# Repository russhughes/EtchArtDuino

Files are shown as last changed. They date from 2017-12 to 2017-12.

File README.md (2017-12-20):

# EtchArtDuino

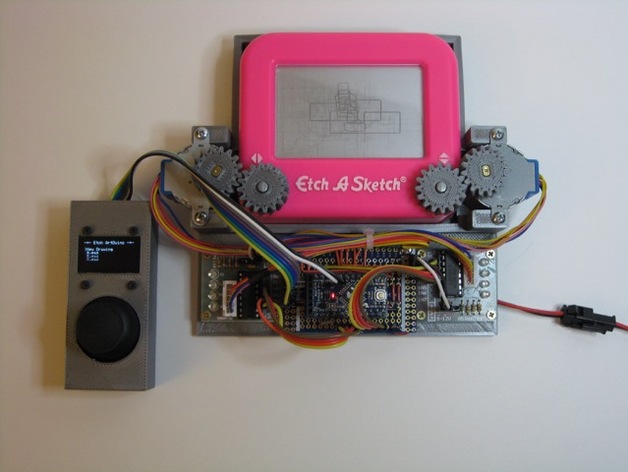
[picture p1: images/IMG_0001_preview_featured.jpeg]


## Description

Arduino powered Etch A Sketch with joystick controller and SD card storage. Arduino source included in EtchArtDuino folder.  The EtchArtDuinoSimple folder contains a simplified version of the software that just allows you to draw using the joystick that is usefull for younger children.

## Instructions

Sorry, not a lot of build details here. I just built as I went with parts I had on hand in order to play with the steppers. It's one of my first OpenSCAD and Arduino projects so the code is, what it is. Don't judge it too harshly.  

The menu system is pretty basic but it allows you to create and save a new drawing and redraw or delete an existing drawing.  

Joystick| Menu usage  
:------:|:----------:
Up/Down | Moves cursor  
Left | Back/Cancel  
Right or Press | Select  

Joystick Drawing usage is as you would expect:up, down, left, right. Press the joystick to end the drawing. It will ask if you are done, select yes to save and exit the drawing or select no to continue drawing.   

Since the Etch ArtDuino has no way of knowing where the drawing stylus is at the beginning of a drawing, the display will ask you to choose a starting position (upper left or right, lower left or right, or the center) and then ask you to move the stylus there then press the joystick. It will save the starting position as the first byte of the file so it can prompt you to move the stylus to the correct position when redrawing the file.  

Drawings are stored on a SD card using the Arduino SD library. You can cheat and create the files on a computer. The files must have an ".eas" extension and be in the root directory.  

    The file format is:  
	
	1st byte is binary and contains the suggested starting position   
		1: Upper Left  
		2: Upper Right  
		3: Lower Left  
		4: Lower Right  
		5: Center  

	The rest of the file is a string of single character   
    drawing commands  

		u: move up  
		d: move down  
		l: move left  
		r: move right  

    An example of a tiny 3x3 box would be:  
    (binary value of 1,2,3,4 or 5)rrrdddllluuu  

### Wiring chart
  
Arduino | Connection
:------:|:---------:
VCC	 | +5V Supply  
GND	 | Ground  
D2	| Horiz/Left Stepper IN1  X-axis  
D3	| Horiz/Left Stepper IN2  
D4	| Horiz/Left Stepper IN3  
D5	| Horiz/Left Stepper IN4  
D6	| Vert/Right Stepper IN1 Y-axis  
D7	| Vert/Right Stepper IN2  
D8	| Vert/Right Stepper IN3  
D9	| Vert/Right Stepper IN4  
D10	 | SPI SS SD Card  
D11	 | SPI MOSI SD Card  
D12	 | SPI MISO SD Card  
D13 | SPI SCK SD Card  
A0 | 	Joystick VX  
A1 | 	Joystick VY  
A2 | 	Joystick Button  
A4 | 	I2C SDA		OLED  
A5 | 	I2C SCL		OLED  

### Parts List:  
Qty | Description
:--:|------------
1 | 3D Printed EtchArtDuino.stl  
1 | 3D Printed gears.stl  
1 | 3D Printed joystick.stl  
1 | Pocket Etch A Sketch  
2 | 28BYJ-48 5V DC 4-Phase 5-Wire + ULN2003 Driver Board (ebay/amazon)  
1 | Catalex microsd card adapter (ebay/electrodragon/amazon)  
1 | Parallax.com Circuit Overlay Board (Part #32999) 
1 | Arduino Pro Mini 328 - 5V/16MHz (sparkfun)  
1 | 0.96" I2C 128X64 OLED (ebay/electrodragon/amazon)  
1 | PS2 Joystick Module marked "Keyes_SJoys" (ebay/electrodragon/amazon)
1 | 5v Power supply and mating connector.  
  Miscellaneous | 2mm screws and nuts. 
Miscellaneous | jumper wires  

### Additional SCAD Sources:  

Parkinbot's Excellent Gear Library http://www.thingiverse.com/thing:636119  

### Additional Arduino Libraries:  

SSD1306Ascii	https://github.com/greiman/SSD1306Ascii  
Bounce2  https://github.com/thomasfredericks/Bounce2

### License
http://www.thingiverse.com/thing:948117
licensed under the Creative Commons - Attribution - Share Alike license. http://creativecommons.org/licenses/by-sa/3.0/

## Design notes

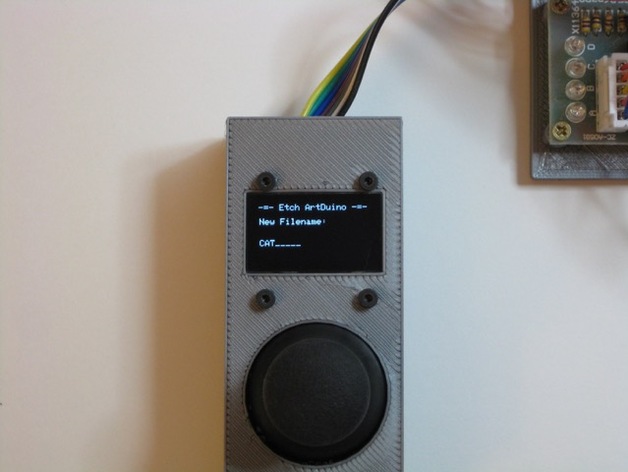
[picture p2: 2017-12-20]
images/IMG_0015_preview_featured.jpeg

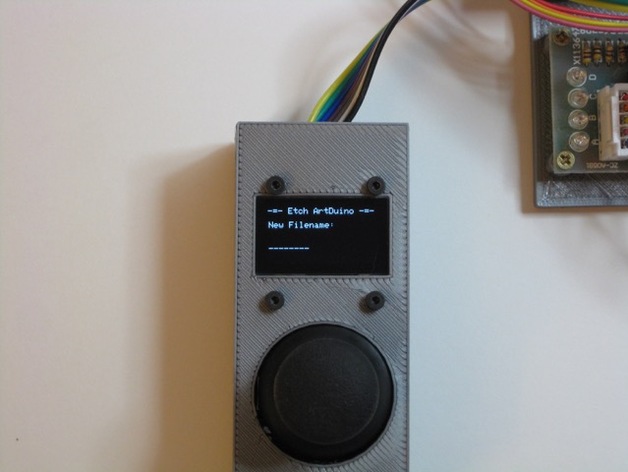
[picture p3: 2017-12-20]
images/IMG_0014_preview_featured.jpeg

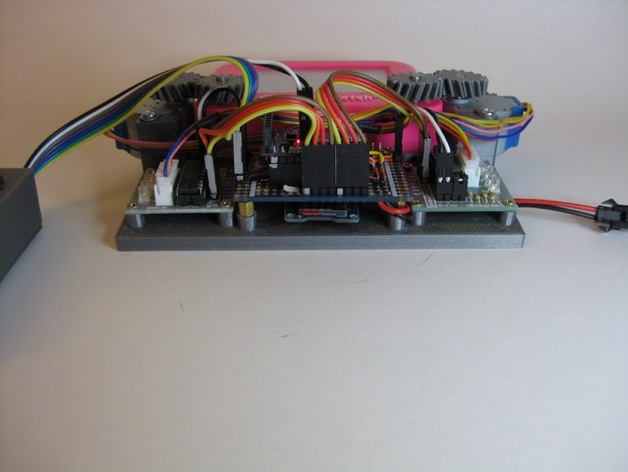
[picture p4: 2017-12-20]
images/IMG_0011_preview_featured.jpeg

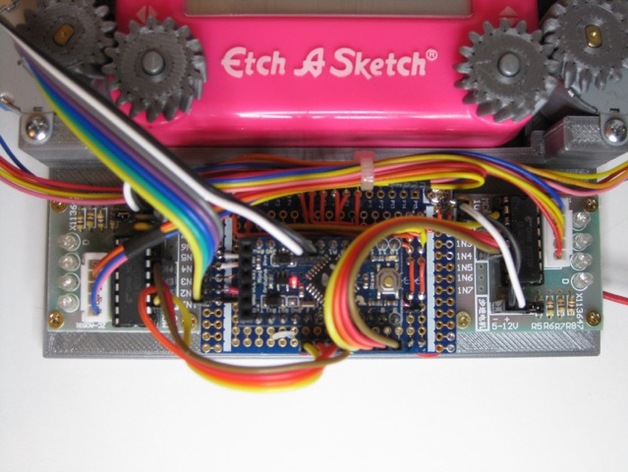
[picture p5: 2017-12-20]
images/IMG_0004_preview_featured.jpeg

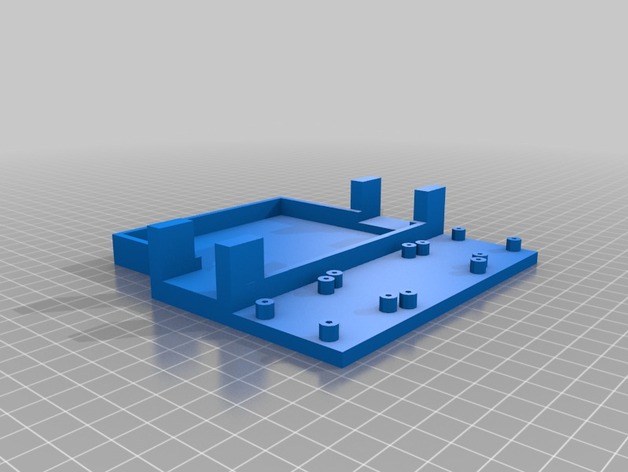
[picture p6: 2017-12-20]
images/EtchArtDuino_preview_featured.jpg

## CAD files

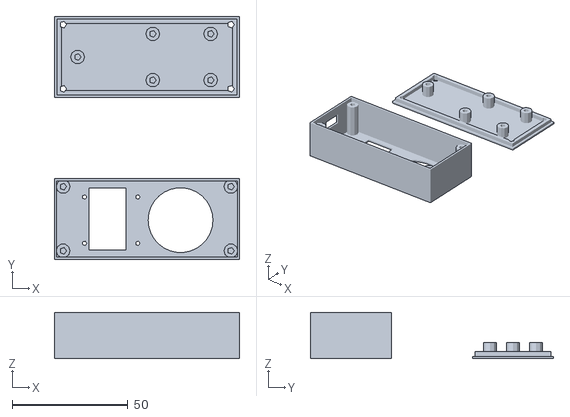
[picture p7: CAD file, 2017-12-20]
3D Printer Files/joystick.stl
80.0 x 105.0 x 20.0

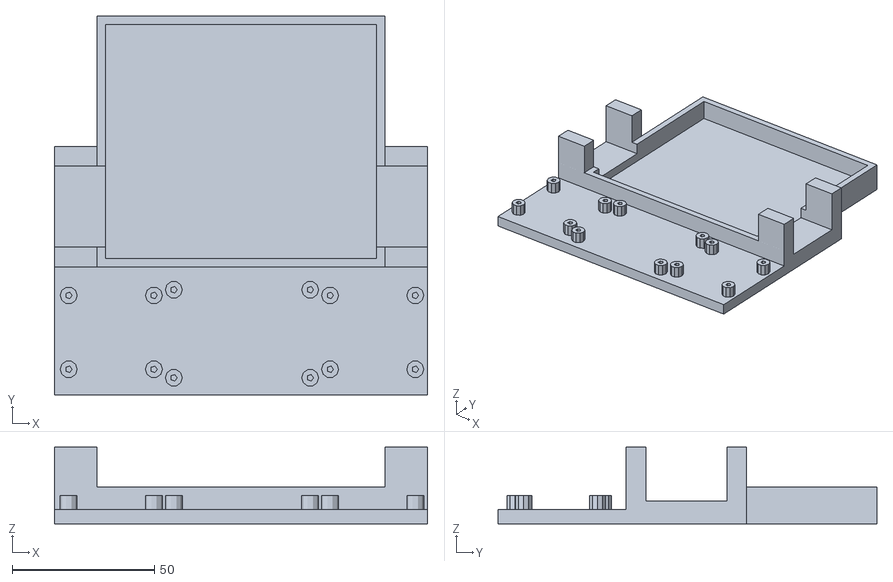
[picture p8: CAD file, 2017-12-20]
3D Printer Files/EtchArtDuino.stl
131.3 x 133.3 x 27.0

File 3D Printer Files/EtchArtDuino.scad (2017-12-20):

height=10;              // height of pocket
width=95.3;             // width of pocket
length=82.3;            // length of pocket
thick=3;                // thickness of wall
supports=5;             // support shelf thickness 

owidth=width+thick*2;   // pocket outside width
olength=length+thick*2; // pocket outside length
oheight=height+thick;   // pocket outside height

so_d = 6;               // stand off diameter
shelf_w = owidth+15+15;          // board shelf width
shelf_l = 45;           // board shelf length

// board stand off

module stand_off()
{
    translate([0,0,-1])
    {
        difference() 
        {
            cylinder(h=6,d=so_d, center= false);
            cylinder(h=6,d=so_d/2.5, center= false);
        }
    }
}

// Servo board holder

module servo_board()
{
    //cube([36, 38, 5]);
    translate([3,9,5]) stand_off();
    translate([3,35,5]) stand_off();
    translate([33,9,5]) stand_off();
    translate([33,35,5]) stand_off();
}

// Cpu board holder

module cpu_board()
{
    //cube([56, 40, 6]);
    translate([4,6,5]) stand_off();
    translate([56-4,6,5]) stand_off();
    
    translate([4,37,5]) stand_off();
    translate([56-4,37,5]) stand_off();
    
}

// Board shelf

module shelf()
{
    translate([0,0,0]) 
    {
        cube([shelf_w, shelf_l, 5]);
        translate([2,0,0]) servo_board();
        translate([130-33-3, 0, 0]) servo_board();
        translate([38, 0, 0]) cpu_board();
    }
}


difference () {
union() {
difference()
{
    cube(size = [owidth,olength,oheight], center = false);
    translate([thick,thick,thick+1]) 
        cube(size = [width,length,height+4], center = false);
}

// left servo base
translate([-15,0,0])
    cube([15,42.5, oheight], center = false);

// left servo mount bottom tower
translate([-15,.05,0])
    cube([15,7, oheight+14], center = false);

// left servo mount top tower
translate([-15,28+7.5,0])
    cube([15,7, oheight+14], center = false);

// left servo controller board
//translate([-5,56.3,0])
//    cube([5,32, supports], center = false);

// right servo base
translate([owidth,0,0])
    cube([15,42.5, oheight], center = false);
    
// right servo mount bottom tower
translate([owidth,.05,0])
    cube([15,7, oheight+14], center = false);
    
// right servo mount top tower
translate([owidth,28+7.5,0]) 
    cube([15,7, oheight+14], center = false);
}

// left servo base servo cutout
translate([-15,7,oheight-5])
    cube([15+thick,28.5, 5], center = false);

// right servo base servo cutout
translate([owidth-thick,7, oheight-5])
    cube([15+thick,28.5, 5], center = false);
}

translate([-15,-shelf_l, 0]) 
    shelf();

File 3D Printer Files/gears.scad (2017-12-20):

// library for parametric involute gears 
// Author: Rudolf Huttary, Berlin 
// Jan 2015

$fn = 500; 
iterations = 10; // increase for enhanced resolution beware: large numbers will take lots of time!

// default values
// z = 10; // teeth - beware: large numbers may take lots of time!
// m = 1;  // modulus
// x = 0;  // profile shift
// h = 4;  // face_width	respectivly axial height
// w = 20; // profile angle
// clearance  // assymmetry of tool to clear tooth head and foot
//    = 0.1; // for external splines
//    = -.1  // for internal splines 
// w_bevel = 45; // axial pitch angle
// w_helix = 45; // radial pitch angle 

// use this prototype:
// gear(m = modulus, z = Z, x = profile_shift, w = alpha, h = face_width);

di = 20; 
knob_r = 2.5-.125;  // took away .2
knob_h = 4;
servo_r = 2.5; // was 2.45 added .250/2 added .250/2 again
servo_h = 4;

// 2 Gears for knobs 

module knob_gear()
{
    difference(){       
        gear_helix(z = 16, m = 1.2, h = knob_h, w_helix = -20, clearance = 0.1); 
        cylinder(h=knob_h,r=knob_r, center= true);
    }
}

translate([di, di, knob_h])     knob_gear();
translate([-di, di, knob_h])    knob_gear();


// 2 gears for servos

module servo_gear() {
    difference(){   
        gear_helix(z = 16, m = 1.2, h = servo_h, w_helix = 20, clearance = 0.1); 
        cylinder(h=servo_h,r=servo_r, center= true);
    }
    
    // keyway
    
    translate([1.7,0-4, -servo_h/2]) cube(size=[3,8,servo_h]);
    translate([-4.7,0-4, -servo_h/2]) cube(size=[3,8,servo_h]);
}

translate([di, -di, servo_h])       servo_gear();
translate([-di, -di, servo_h])      servo_gear();

//
// Abandon hope all ye who edit past this comment !!!
//

// === modules for internal splines
module Gear(m = 1, z = 10, x = 0, h = 4, w = 20, D = 13, clearance = -.1, center = true) 
{
   difference()
   {
		cylinder(r = D/2, h = h, center = center);
		gear(m, z, x, h+1, w, center = center, clearance = clearance); 
	}
}

module Gear_herringbone(m = 1, z = 10, x = 0, h = 4, w = 20, w_helix = 45, D = 13, clearance = -.1) 
{
   difference()
   {
		cylinder(r = D/2, h = h-.01, center = true); // CSG!
		gear_herringbone(m, z, x, h, w, w_helix, clearance = clearance); 
	}
}

module Gear_helix(m = 1, z = 10, x = 0, h = 4, w = 20, w_helix = 45, D = 13, clearance = -.1) 
{
   difference()
   {
		cylinder(r = D/2, h = h-.01, center = true); // CSG!
		gear_helix(m, z, x, h, w, w_helix, clearance = clearance); 
	}
}

module Gear_bevel(m = 1, z = 10, x = 0, h = 4, w = 20, w_bevel = 45, w_helix = 0, D = 13, clearance = -0.1, center = true)
{
   rotate([0, 180, 0])
   difference()
   {
		cylinder(r = D/2, h = h-.01, center = true); // CSG!
		gear_bevel(m, z, x, h, w, w_bevel, w_helix, clearance = clearance, center = center); 
	}
}


// === modules for external splines
module gear_herringbone(m = 1, z = 10, x = 0, h = 4, w = 20, w_helix = 45, clearance = 0.1)
{
   for(i=[0, 1])
   mirror([0,0,i])
   translate([0, 0, -0.001]) // CSG!
   gear_helix(m, z, x, h/2, w, w_helix, center = false, clearance = clearance); 
}

module gear_helix(m = 1, z = 10, x = 0, h = 4, w = 20, w_helix = 45, center = true, clearance = 0.1)
{
   gear_info(m, z, x, h, w, w_helix, 0, clearance); 
	r_wk = m*z/2 + x; 
   tw = (h * w_helix)/ r_wk  ; 
	linear_extrude(height = h, center = center, twist = tw, slices = ceil(10*h), convexity = z)
   gear_(m, z, x, w, clearance); 
}

module gear_bevel(m = 1, z = 10, x = 0, h = 4, w = 20, w_bevel = 45, w_helix = 0, clearance = 0.1, center = true)
{
   gear_info(m, z, x, h, w, 0, w_bevel, clearance); 
	r_wk = m*z/2 + x; 
   sc = (r_wk-tan(w_bevel)*h)/r_wk; 
   tw = (h * w_helix)/ r_wk  ; 
	linear_extrude(height = h, center = center, twist = tw, scale = [sc, sc], convexity = z)
   gear_(m, z, x, w, clearance); 
}

module gear(m = 1, z = 10, x = 0, h = 4, w = 20, clearance = 0.1, center = true)
{
   gear_info(m, z, x, h, w, clearance = clearance); 
	linear_extrude(height = h, center = center, convexity = z)
   gear_(m, z, x, w, clearance); 
}

module gear_info(m = 1, z = 10, x = 0, h = 0, w = 20, helix_angle = 0, bevel_angle = 0, clearance = 0.1)
{
  	r_wk = m*z/2 + x; 
   	dy = m;  
  	r_kk = r_wk + dy;   
  	r_fk = r_wk - dy;  
  	r_kkc = r_wk + dy *(1-clearance/2);   
  	r_fkc = r_wk - dy *(1+clearance/2);  
   echo(str ("modulus = ", m)); 
   echo(str ("Z = ", z)); 
   echo(str ("profile angle = ", w, "°")); 
   echo(str ("d = ", 2*r_wk)); 
   echo(str ("d_outer = ", 2*r_kk, "mm")); 
   echo(str ("d_inner = ", 2*r_fk, "mm")); 
   echo(str ("height = ", h, "mm")); 
   echo(str ("clearance factor = ", clearance)); 
   echo(str ("d_outer_cleared = ", 2*r_kkc, "mm")); 
   echo(str ("d_inner_cleared = ", 2*r_fkc, "mm")); 
   echo(str ("helix angle = ", helix_angle, "°")); 
   echo(str ("bevel angle = ", bevel_angle, "°")); 
   echo("================"); 
}

// === from here 2D stuff == 
module gear_(m = 1, z = 10, x = 0, w = 20, clearance = 0.1)
{
  	r_wk = m*z/2 + x; 
   	dy = m;  
  	r_fkc = r_wk - dy *(1+clearance/2)+.01;  //.01 has numerical reason!
   union()
	{
		for(i = [0:z-1]) 
			rotate([0, 0, i*360/z])
			Tooth(m, z, x, w, clearance);
     circle(r_fkc); 
	}
}

module Tooth(m = 1, z = 10, x = 0, w = 20, clearance = 0)
{
	union()
	{
		Tooth_half(m, z, x, w, clearance); 
		mirror([1, 0, 0])
		Tooth_half(m, z, x, w, clearance); 
	}
}

module Tooth_half(m = 1, z = 10, x = 0, w = 20, clearance = 0)
{
  	r_wk = m*z/2 + x; 
  	r_fkc = r_wk - m *(1+clearance/2);   
	du = z*m/360*PI; 
	dw = 360/z; 
 	difference()
	{
		cake_piece(m, z, x, w, clearance); 
      	union()
		{
			for(i = [-dw:dw/iterations:dw])
			  rotate([0, 0, i])
			  translate([i*du, 0, 0])
			Tool(m, z, x, w, clearance); 
		}
	}
}

module Tool(m = 1, z = 10, x = 0, w = 20, clearance = 0)
{
   p = m*PI; 
   dy = 2*m;  
   dx = dy * tan(w);  
   ddx = dx/2 * clearance/2; 
   ddy = dy/2 * clearance/2; 
	r_wk = m*z/2 + x; 
   polygon(points = [
		[0, r_wk+dy], 
		[0, r_wk+dy/2-ddy], 
		[p/4-dx/2 + ddx, r_wk+dy/2 - ddy], 
		[p/4+dx/2 + ddx, r_wk-dy/2 - ddy], 
		[p/2,            r_wk -dy/2 - ddy],
		[p/2,            r_wk +dy/2 - ddy],
		[p/2,            r_wk+dy], 
		]);  
}

module cake_piece(m = 1, z = 10, x = 0, w = 20, clearance = 0)
{
	$fn = 100; 
	r_wk = m*z/2 + x; 
   p = m*PI; 
   dy = p/2*cos(w);  
   r_kk = r_wk + dy*(1+clearance);   
   intersection()
   {
     half_circle(r_kk); 
     rotate([0, 0, 180])
     rotate([0, 0, -181/z]) // 181 has numerical reason!
     half_circle(r_kk); 
	}
}

module half_circle(r)
{
	intersection()
  	{
		circle(r = r); 
     translate([0, -r, 0])
     square(2*r); 
	}
}

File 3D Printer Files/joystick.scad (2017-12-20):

length = 80;            // box lenght
width = 35;             // box width
height = 20;            // box, height

joy = 28;               // joystick hole diameter
joy_offset = 15;         // x offset for joysitck

so_d = 6;               // stand off diameter

disp_offset = 15;        // display offset from end
disp_w = 27;            // display width
disp_l =16;             // display length

disp_hdist = 20;        // display horizontal mounting hole distance
disp_vdist =  23;       // display vertial mount hole distance

module standoff(sh=6, sd=6)
{
    translate([0,0,-1])
    {
        difference() 
        {
            // standoff
            
            cylinder(h=sh,d=sd, center= false);
            
            // screw hole
            
            cylinder(h=sh,d=sd/2, center= false);
        }
    }
}

module base() 
{
    // four standoffs for joystick (25x20mm) 
    
    translate([0,0,0])      standoff(sh=7, sd=so_d);
    translate([25,0,0])     standoff(sh=7, sd=so_d);
    translate([0,20,0])     standoff(sh=7, sd=so_d);
    translate([25,20,0])    standoff(sh=7, sd=so_d);
}    

module wire()
{
    cube([2,10,5]);
}

module box()
{
    difference()
    {
        // outer shell
        
        cube([length, width, height]);
        
        // inner wall
        
        translate([1,1,1])
            cube([length-2, width-2, height]);
        
        // wire hole
        
        translate([0,width/2-5, 10])
            wire();

        // Joystick hole
        
        translate([length/2+joy_offset-0.5,width/2-0.5,0])
            cylinder(h=2,d=joy, center=false);
        
        // display hole
        
        translate([disp_offset ,width/2-disp_w/2,0])    cube([disp_l,disp_w,1]);
        
        // display mounting holes
        
        translate([disp_offset ,width/2-disp_w/2,0])
        {
            translate([-2,3,0])     cylinder(h=1,d=2, center= false);
            translate([-2,23,0])    cylinder(h=1,d=2, center= false);
            translate([-2+23,3,0])  cylinder(h=1,d=2, center= false);
            translate([-2+23,23,0]) cylinder(h=1,d=2, center= false);
        }
    }
    
    // corner standoffs
    
    translate([5-1.25,5-1.25,1]) standoff(sh=height-2.1, sd=so_d);
    translate([5-1.25,30+1.5,1]) standoff(sh=height-2.1, sd=so_d);
    
    translate([length-3.75,5-1.25,1]) standoff(sh=height-2.1, sd=so_d);
    translate([length-3.75,30+1.5,1]) standoff(sh=height-2.1, sd=so_d);
    
    // proto board standoff
    

}

module bottom()
{
    difference()
    {
        // bottom
        
        union() 
        {
            cube([length, width, 1]);
        
            // joystick mounting base

            translate([length/2-25/2+joy_offset, width/2-20/2,1]) 
                base();
            
            // protoboard standoff
            
            translate([10,width/2,1]) standoff(7, sd=so_d);

    
            // lengthwise bottom ridges
    
            translate([1.1,1.1,1])       cube([length-2.2, 2, 2]);
            translate([1.1,width-3.1,1]) cube([length-2.2, 2, 2]);
    
            // horizontal botton ridges
    
            translate([1.1,1.1,1])         cube([2, width-2.2, 2]);
            translate([length-3.1,1.1,1])  cube([2, width-2.2, 2]);
        }  
        
        // standoff screw holes
        
        translate([5-1.25,5-1.25,0])        cylinder(h=5,d=so_d/2, center= false);
        translate([5-1.25,30+1.5,0])        cylinder(h=5,d=so_d/2, center= false);
        translate([length-3.75,5-1.25,0])   cylinder(h=5,d=so_d/2, center= false);
        translate([length-3.75,30+1.5,0])   cylinder(h=5,d=so_d/2, center= false);
    }

   
}

box();
translate([0, width*2, 0])   bottom();

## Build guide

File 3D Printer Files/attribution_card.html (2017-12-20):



# Etch ArtDuino by PawArmy

## Published on July 30, 2015

### www.thingiverse.com/thing:948117

####   

#### Creative Commons - Attribution - Share Alike

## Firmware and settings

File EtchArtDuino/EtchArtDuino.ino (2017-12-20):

/*
 * Etch-Art-Duino
 *  
 * Russ Hughes, July 2015 russ@owt.com 
 * Creative Commons - Attribution - Non-Commercial license.
 * 
 */

#include <SPI.h>
#include <SD.h>
#include <Wire.h>
#include "SSD1306Ascii.h"
#include "SSD1306AsciiWire.h"
#include <Stepper.h>
#include <Bounce2.h>
#include "menu.h"

// display 
#define I2C_ADDRESS 0x3C
SSD1306AsciiWire oled;
#define DISPLAY_LINES 8
#define MENU_LINES 6

// sd card

const int PIN_SD_CS = 10;
const bool ALLOW_WIPE = false;
char fileName[13];
char fileNames[MENU_LINES][13];  
int	fileCount = 0;
File dir;

// steppers

Stepper horiz(4076, 2, 4, 3, 5);  // left + / right -
Stepper vert(4076, 6, 8, 7, 9);   // up- / down +

// buttons

#define JOY_UP 3	
#define JOY_DOWN -3
#define JOY_LEFT -3
#define JOY_RIGHT 3

#define X_OFFSET 8
#define Y_OFFSET 14
#define BUTTON A2

Bounce Button = Bounce();

// scale for the drawing commands 1 move command = 5 steps

int scale = 5;

//
// motorOff: turn off stepper motors
//

void motorOff() {
	for (int i = 2; i < 10; i++)
		digitalWrite(i, LOW);
}

//
// displayInit: initalize oled display
//

void displayInit()
{
	Wire.begin();         
	oled.begin(&Adafruit128x64, I2C_ADDRESS);
	oled.set400kHz();  
	oled.setFont(Adafruit5x7);
	oled.clear();
}

//
// setup: Rememeber when this used to be called main()
//

void setup()
{
	motorOff();
	displayInit();

	// stepper speed, 5 seems to work well without missing steps
	
	horiz.setSpeed(5);
  	vert.setSpeed(5);

	// center button on joystick
	
  	pinMode(BUTTON, INPUT_PULLUP);
  	Button.attach(BUTTON);
  	Button.interval(25);

	// initalize sd card and open root directory
  
	pinMode(PIN_SD_CS, OUTPUT);
  	if (SD.begin(PIN_SD_CS))
  	{
  		dir = SD.open("/");
  		if (dir)
    		mainMenu();
    	else
    		oled.println(F("Cant open /"));
  	}
  	else 
    	oled.println(F("SD Card Failure!"));
}

// 
// isEtchFile - if fileName is an ".eas" file return the fileName string length
//  otherwise return 0
//

int isEtchFile(char *filename)
{
  	int len = strlen(filename);
  	if (len > 4)
  	{
    	if (!strstr(strlwr(filename+(len-4)), ".eas"))
      		len = 0;      
  	}
  	else
    	len = 0;
    
  	return len;
}

//
// countFiles: returns the number of the EAS files in the root directory.
//

int countFiles()
{
	File entry;
	int files = 0;	

  	if (dir)
  	{
  		dir.rewindDirectory();
  	
      	while (entry = dir.openNextFile())
      	{
      		strcpy(fileName,entry.name());
      		
        	if (isEtchFile(fileName))	
          		files++;
          	entry.close();
      	}
  	}
  	return files;	
}

//
//	listFiles: List's EAS files in root directory on oled 
//
//		first - number of first file to display
//		line - currently selected line number
//		lines - number of lines to display
//

void listFiles(int first, int line, int lines)
{
	File entry;
	int	count = 0;
  	int file = 0;

  	if (first == 0)
  	{
		strcpy(fileNames[0], "");
  		oled.setCursor(1, 2);
  		if (line == 0) 
  			oled.print(">");
  		else
  			oled.print(" ");
  			
  		oled.print(F("New Drawing"));
  		oled.clearToEOL();
  		count = 1;
  	}
  	
  	if (dir)
  	{
  		dir.rewindDirectory();
      	while (entry = dir.openNextFile())
      	{
        	strcpy(fileName,entry.name());
        	if (isEtchFile(fileName))
        	{	
          		file++;

          		if (file >= first)
          		{
              		if (count < lines)
              		{
              			strcpy(fileNames[count], fileName);
              			oled.setCursor(1,count+2);	

                		if (line == count)
                			oled.print(">");
                		else
                			oled.print(" ");
                			
                		oled.print(fileName);    
                		oled.clearToEOL();
                		count++;
              		}
              		else
              		{
              			
              			entry.close();
                		break;
              		}
            	}
        	}
        	entry.close();
		}
		
		while (count < lines)
  		{
  			oled.setCursor(1,count+2);
  			oled.clearToEOL();
  			count++;
		}
  	}
  	else
		oled.print(F("SD Card Read Failure!"));
}

//
// cls: clear display and show banner
//

void cls()
{
	oled.clear();
  	oled.println(F("-=- Etch ArtDuino -=-"));
  	oled.setCursor(1,2);
}

//
// Menus, menus, menus
//

#define YN_yes 1
#define YN_no 0

int ynMenu(const __FlashStringHelper *title, char *data)
{
	MENU menu[] =
	{
		{ F("Yes"), YN_yes 	},
		{ F("No"), 	YN_no  	},
		{ NULL,		0		}
	};

	return displayMenu(menu, title, fileName);
}

#define FM_draw 1
#define FM_delete 2
#define FM_cancel 0

int fileMenu(const __FlashStringHelper *title, char *data)
{
	MENU menu[] =
	{
		{ F("Draw File"),	FM_draw 	},
		{ F("Delete File"),	FM_delete 	},
		{ F("Cancel"),		FM_cancel 	},
		{ NULL, 			0 			}
	};

	return displayMenu(menu, title, fileName);	
}

#define START_ULEFT 1
#define START_URIGHT 2
#define START_LLEFT 3
#define START_LRIGHT 4
#define START_CENTER 5
#define START_CANCEL 0

int startMenu(const __FlashStringHelper *title, char *data)
{
	MENU menu[] =
	{
		{ F("Upper Left"), 	START_ULEFT 	},
		{ F("Upper Right"), START_URIGHT 	},	
		{ F("Lower Left"), 	START_LLEFT 	},	
		{ F("Lower Right"), START_LRIGHT 	},	
		{ F("Center"), 		START_CENTER 	},	
		{ F("Cancel"), 		START_CANCEL 	},		
		{ NULL,				0				}
	};
	
	return displayMenu(menu, title, fileName); 
}

//
// mainMenu: display main menu
//

void mainMenu()
{
	int	again = 1;
	int	waiting = 1;
  	int count = 0;
  	int	line = 0;
  	int	first = 0;
  	int	vx;
  	int	vy;

  	cls();
  	fileCount = countFiles();
	
  	while (again)
  	{
  		listFiles(first, line, MENU_LINES);
  	
  		if (!waiting)
		{
			delay(250);
			waiting = 1;
		}
		
		while (waiting)
		{
  			vx = map(analogRead(A0)+X_OFFSET,0, 1023, 3, -3);    // read the input pin
  			if (vx == JOY_UP)	// up
  			{
  				waiting = 0;
  				if(line >0)
  					line--;
  				else
  					if (first)
  						first--;
  			}
  		
  			if (vx == JOY_DOWN)	// down
  			{
  				waiting = 0;
  				if (line < MENU_LINES-1 && line < fileCount)
  					line++;	
  				else
  					if (first <= fileCount - MENU_LINES)
  						first++;
  			}
  			
  			vy = map(analogRead(A1)+Y_OFFSET,0, 1023, 3, -3);    // read the input pin
 			
 			Button.update();
  			if (Button.read() == LOW)
  			{
  				waitButton();
  				vy = JOY_RIGHT;
  			}
  			
   			if (vy == JOY_RIGHT)		// right
  			{
  				waitY();
  					
  				if (fileNames[line][0] != 0)
  				{
  					switch (fileMenu(F("File: "), fileNames[line]))
  					{
  						case FM_draw:
  							drawFile(fileNames[line]);
  							break;
  							
  						case FM_delete: 
  							if (ynMenu(F("Delete: "), fileNames[line]))
  							{
  								SD.remove(fileNames[line]);
  								fileCount = countFiles();
	  							line = 0;
  								first = 0;
  							}
  							break;
  					}
  					cls();
  				}
				else
				{
					newFile();
					fileCount = countFiles();
					cls();
				}
  				waiting = 0;
  			}
		}
  	}
}

//
// waitX: waits until joystick x axis is returned to center
//

void waitX()
{
	while (map(analogRead(A0)+X_OFFSET,0, 1023, 3, -3) != 0)    // read the input pin
		delay(100);
}

//
// waitY: waits until joystick y axis is returned to center
//

void waitY()
{
	while (map(analogRead(A1)+Y_OFFSET,0, 1023, 3, -3) != 0)    // read the input pin
		delay(100);
}

//
// waitButton: waits until the button is released
//
void waitButton()
{
	while (Button.read()== LOW) 
    	Button.update();
}

//
// drawFile: draws given filename
//

void drawFile(char *filename)
{
	File  dataFile;
	unsigned long fileSize;
	long current = 0;
	byte start;
  	char ch;

	waitY();
	cls();
			
  	dataFile = SD.open(filename); 
  	if (dataFile) 
  	{
  		start = dataFile.read();
		if (start)
		{
			if (moveToStart(start))
			{
				oled.print(F("Drawing:\n  "));
				oled.println(filename);
				oled.println("");

		  		fileSize = dataFile.size();
	  			oled.print(F("Length:  "));
				oled.println(fileSize);
		
    			while (dataFile.available()) 
    			{
      				ch = dataFile.read();
      				current++;
   		
	      			switch(ch)
    	  			{
	        			case 'u' : moveup();  break;      
        				case 'd' : movedown();  break;      
        				case 'l' : moveleft();  break;      
        				case 'r' : moveright();  break;      
      				}
    			}
				dataFile.close();
				motorOff();
			}
		}
	}
	else 	// if the file isn't open, pop up an error:
	{
    	oled.println(F("error opening "));
    	oled.println(filename);
  	}
}

// moveup: moves drawing stylus up scale steps

void moveup() 
{
	vert.step(-scale);
}

// movedown: moves drawing stylus down scale steps

void movedown() 
{
	vert.step(scale);
}

// moveleft: moves drawing stylus left scale steps

void moveleft() 
{
	horiz.step(scale);
}

// moveright: moves drawing styles right scale steps

void moveright()
{
	horiz.step(-scale);
}

//
//	nameFile: Prompts user to enter filename using joystick
//

int nameFile()
{
	int	again = 1;
	int rc = 0;
	int vx, vy;
	int letter = 0;
	char c;
	int	i;
	unsigned long blinkTime = millis();;
	int blink = 0;
		
	memset(fileName, 0, sizeof(fileName));
	
	cls();
	oled.println(F("New Filename:"));
		
	while (again)
	{
		if (millis() - blinkTime > 250)
		{
			blinkTime = millis(); 
			blink = !blink;
		}
		
		oled.setCursor(1,5);
		for (i = 0; i < 8; i++)
		{
			if (fileName[i])
				c = fileName[i];
			else
				c = '_';	

			if (blink && letter == i)
				c = ' ';

			oled.write(c);
		}
			
		vx = map(analogRead(A0)+X_OFFSET,0, 1023, 3, -3);    // read the input pin
  		vy = map(analogRead(A1)+Y_OFFSET,0, 1023, 3, -3);    // read the input pin
			
  		if (vx == JOY_UP)		// up 
  		{
  			waitX();
  			if (fileName[letter])
  			{
  				if (fileName[letter] != '_')
  				{
  					fileName[letter]++;
  					if (fileName[letter] > 'Z')
  						fileName[letter] = '_';
  				}
  				else
  					fileName[letter] = 'A';
  			}
  			else
  				fileName[letter] = 'A';
  		}
  		
  		if (vx == JOY_DOWN)		// down
  		{
  			waitX();
  			if (fileName[letter])
  			{
  				if (fileName[letter] != '_')
  				{
  					fileName[letter]--;
  					if (fileName[letter] < 'A')
  						fileName[letter] = '_';	
  				}
  				else
  					fileName[letter] = 'Z';
  			}
  			else
  				fileName[letter] = 'Z';
  		}
  		
  		if (vy == JOY_LEFT)		// left
  		{
  			waitY();
  			if (!letter)
			{
				rc = 0;
				again = 0;
			}
			else
				letter--;  			
		}
  		
  		if (vy == JOY_RIGHT)	// right
  		{
  			waitY();
  			if (fileName[letter])
  			{
  				if (letter < 7)
  					letter++;
  				else
  					letter = 0;
  			}
  		}

		Button.update();
  		if (Button.read() == LOW)
  		{
  			strlcat(fileName, ".EAS", sizeof(fileName));
    		waitButton();
      		again = 0;
      		rc = 1;
  		}
	}
	return rc;
}

//
// newInstructions: display instructions for new drawing
//

void newInstructions()
{
	cls();
	oled.setCursor(0, 3);
	oled.print(F("File: "));
	oled.println(fileName);
	oled.setCursor(0, 5);
	oled.println(F("Use joystick to draw"));
	oled.print(F("then press to end"));
}

//
// moveToStart
//

int moveToStart(byte start)
{
	int again = 1;
	int	rc = 0;
	int vx, vy;

	cls();
	
	oled.print(F("Move stylus to:"));
	oled.setCursor(0,3);
	
	switch (start)
	{
		case START_ULEFT: 
			oled.println(F("Upper Left"));
			break;	
			
		case START_URIGHT:
			oled.println(F("Upper Right"));
			break;	
			
		case START_LLEFT:
			oled.println(F("Lower Left"));
			break;	
			
		case START_LRIGHT:
			oled.println(F("Lower Right"));
			break;	
			
		case START_CENTER:
			oled.println(F("Center"));
			break;	
	}

	oled.setCursor(0,5); 
	oled.println(F("Press to continue"));
	 
	while (again)
	{
		vx = map(analogRead(A0)+X_OFFSET,0, 1023, 3, -3);    // read the input pin
		vy = map(analogRead(A1)+Y_OFFSET,0, 1023, 3, -3);    // read the input pin
	
		if (vx == JOY_UP)
	    	moveup();
  				
  		if (vx == JOY_DOWN)
    		movedown();

  		if (vy == JOY_LEFT)
    		moveleft();
  				
  		if (vy == JOY_RIGHT)
    		moveright();

		Button.update();
   		if (Button.read() == LOW)
  		{
			waitButton();

      		rc = ynMenu(F("Continue? "), fileName);
			again = 0;
		}
	}
	return rc;
}		

//
// newFile: asks user for new filename and records drawing 
//

void newFile()
{
	int again = 1;
	int vx, vy;
	byte start = 0;
	
	if (nameFile())
	{
		if (start = startMenu(F("Choose Start Location:"), NULL))
		{
			if (moveToStart(start))
			{
				newInstructions();
	
				File  dataFile = SD.open(fileName, FILE_WRITE);
				if (dataFile)
				{
					dataFile.write(start);
					while (again)
					{
		  				vx = map(analogRead(A0)+X_OFFSET,0, 1023, 3, -3);    // read the input pin
  						vy = map(analogRead(A1)+Y_OFFSET,0, 1023, 3, -3);    // read the input pin
	
  						if (vx == JOY_UP)
  						{	
		  					dataFile.write('u');
	    					moveup();
  						}
  				
	  					if (vx == JOY_DOWN)
  						{
		  					dataFile.write('d');
    						movedown();
  						}
  				
  						if (vy == JOY_LEFT)
  						{
	  						dataFile.write('l');
    						moveleft();
  						}
  				
  						if (vy == JOY_RIGHT)
  						{
	  						dataFile.write('r');
    						moveright();
  						}

						Button.update();
   						if (Button.read() == LOW)
  						{
		    				waitButton();

      						if (ynMenu(F("Finished? "), fileName))
      						{
		      					again = 0;
		      					dataFile.close();
		      					motorOff();
      						}
      						else
      							newInstructions();
	  					}
					}
				}
			}
		}
	}
	else
	{
		oled.println("Error creating file");
		delay(1000);
	}
}		

//
// Empty
//

void loop()
{ 
}

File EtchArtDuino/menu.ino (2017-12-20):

//
// displayMenu
//

int displayMenu(MENU menu[], const __FlashStringHelper *title, char *data)
{
	int menuCount = 0;
	int	again = 1;
	int	waiting = 1;
	int	first = 0;
  	int count = 0;
  	int	line = 0;
  	int	rc = 0;
  	int	i;
  	int	vx;
  	int	vy;

	oled.clear();
	oled.print(title);
	if (data)
		oled.print(data);
	
	while(menu[i++].option)
		menuCount++;

  	while (again)
  	{
  		count = 0;
  		i = 0;	
  		
		while(menu[i].option)
		{
			if (i >= first)
			{
				if (count < MENU_LINES)
				{
					oled.setCursor(1,count+2);	
               		if (line == count)
               		{
               			oled.print(">");
               			rc = menu[i].value;
               		}
               		else
               			oled.print(" ");
                			
               		oled.print(menu[i].option);    
               		oled.clearToEOL();
					count++;	
				}
			}
			i++;
		}

  		while (count < MENU_LINES)
  		{
  			oled.setCursor(1,count+2);
  			oled.clearToEOL();
  			count++;
  		}
  		
  		if (!waiting)
		{
			delay(250);
			waiting = 1;
		}
		
		while (waiting)
		{
  			vx = map(analogRead(A0)+X_OFFSET,0, 1023, 3, -3);    // read the input pin
  			if (vx == JOY_UP)
  			{
  				waiting = 0;
  				if(line >0)
  					line--;
  				else
  					if (first)
  						first--;
  			}
  		
  			if (vx == JOY_DOWN)
  			{
  				waiting = 0;
  				if (line < MENU_LINES-1)
  					line++;	
  				else
  					if (first <= menuCount - MENU_LINES)
  						first++;
  			}
  			
  			vy = map(analogRead(A1)+Y_OFFSET,0, 1023, 3, -3);    // read the input pin
  			if (vy == JOY_LEFT)
  			{
  				waitY();
  				waiting = 0;
  				again = 0;
  				rc = 0;
  			}
  			
  			if (vy == JOY_RIGHT)
  			{
  				waitY();
  				waiting = 0;
  				again = 0;
  			}
  			
  			Button.update();
  			if (Button.read() == LOW)
  			{
    			waitButton();
      			waiting = 0;
      			again = 0;
      		
  			}
		}
  	}
  	return rc;
}
